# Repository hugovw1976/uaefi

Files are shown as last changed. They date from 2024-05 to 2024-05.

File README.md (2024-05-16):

# Ultra Affordable EFI

🟢[$100 base model rusEFI store](https://www.shop.rusefi.com/shop/p/uaefi-ultra-affordable-efi)🟢

## Community Support

🔴Community support ONLY 🔴 https://www.facebook.com/groups/rusEfi 🔴 [Discord](https://github.com/rusefi/rusefi/wiki/Discord)🔴

## Technical Details

Open Source KiCAD 7 hardware powered by [Hellen-One](https://github.com/andreika-git/hellen-one)

powerted by [rusEFI firmware](https://github.com/rusefi/rusefi)

[User Documentation](https://github.com/rusefi/rusefi/wiki/uaEFI)

x

x

## MCU options

1mg of flash is _required_.

One day we shall try https://jlcpcb.com/partdetail/Stmicroelectronics-STM32F427VIT6%2FC57097#EC or https://jlcpcb.com/partdetail/Stmicroelectronics-STM32F437VIT7%2FC1338578#EC

## rusEFI Store

https://www.shop.rusefi.com/shop/p/uaefi-ultra-affordable-efi

## HOWTO JLCPCB

You would need three files from ``boards/uaefi-a/board`` folder to place your JLCPB Assembly order: gerber.zip BOM-JLC.csv and CPL.csv

### Q: Something wrong with BOM?

A: Nope, that's normal nothing to worry about click 'Continue'.



### Q: how do I get more RAM for Lua?

A: fabricate with STM32F42xVI firmware would defect extra RAM and give you extra Lua. Once your script does not fit into STM32F42xVI it's F7 time or help us leverage F413.

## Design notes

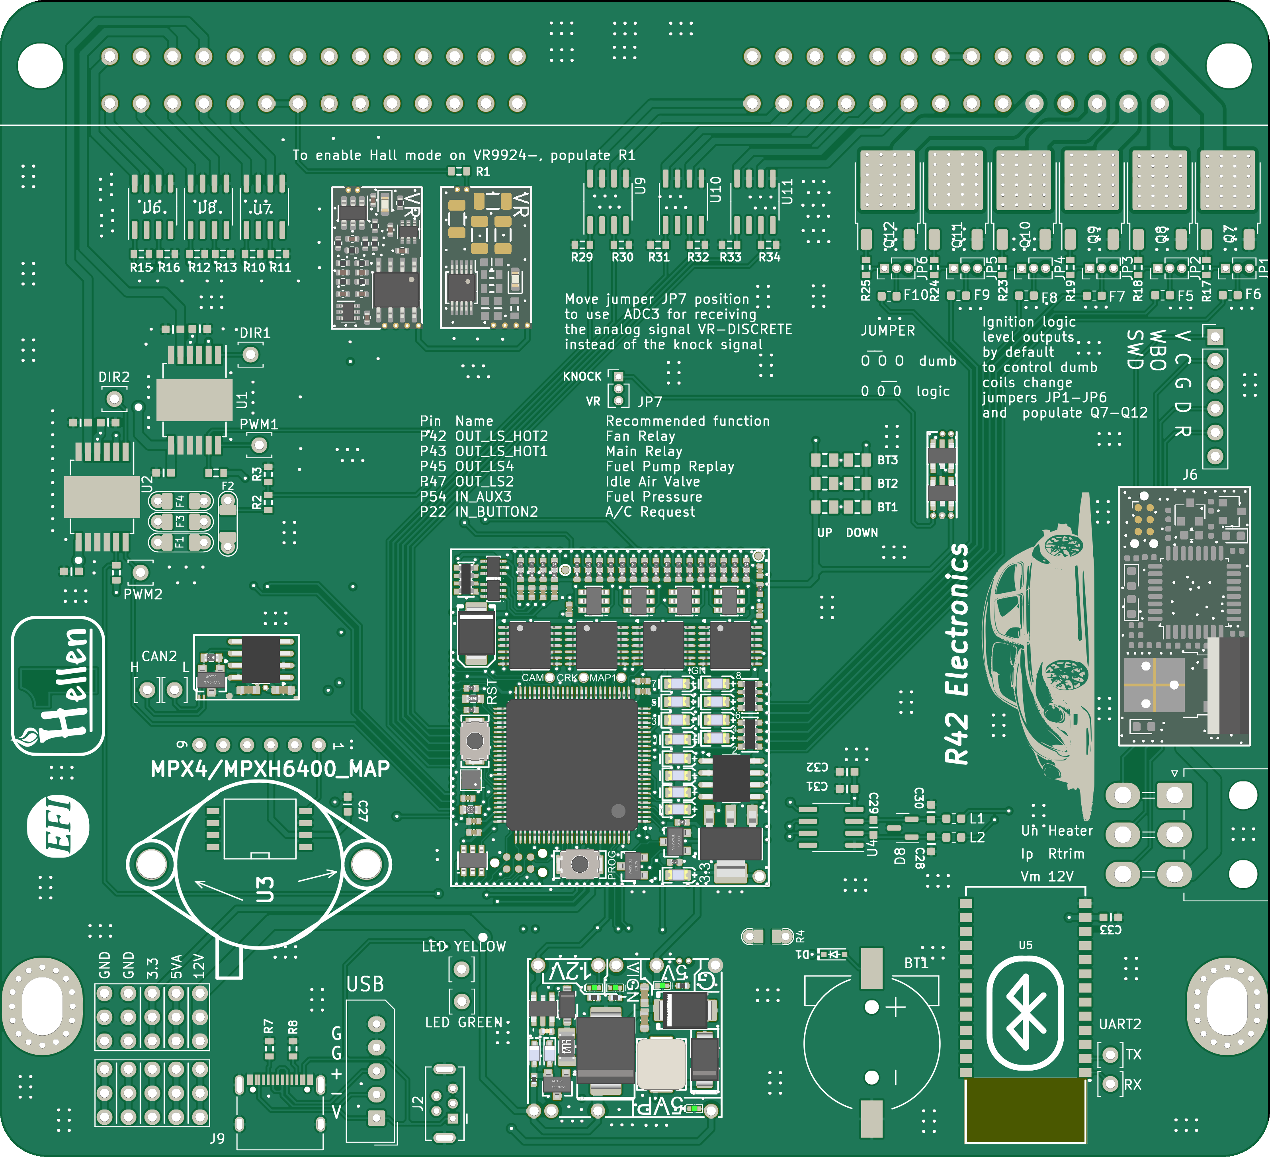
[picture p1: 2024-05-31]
boards/uaefi-d/board/uaefi-d.png

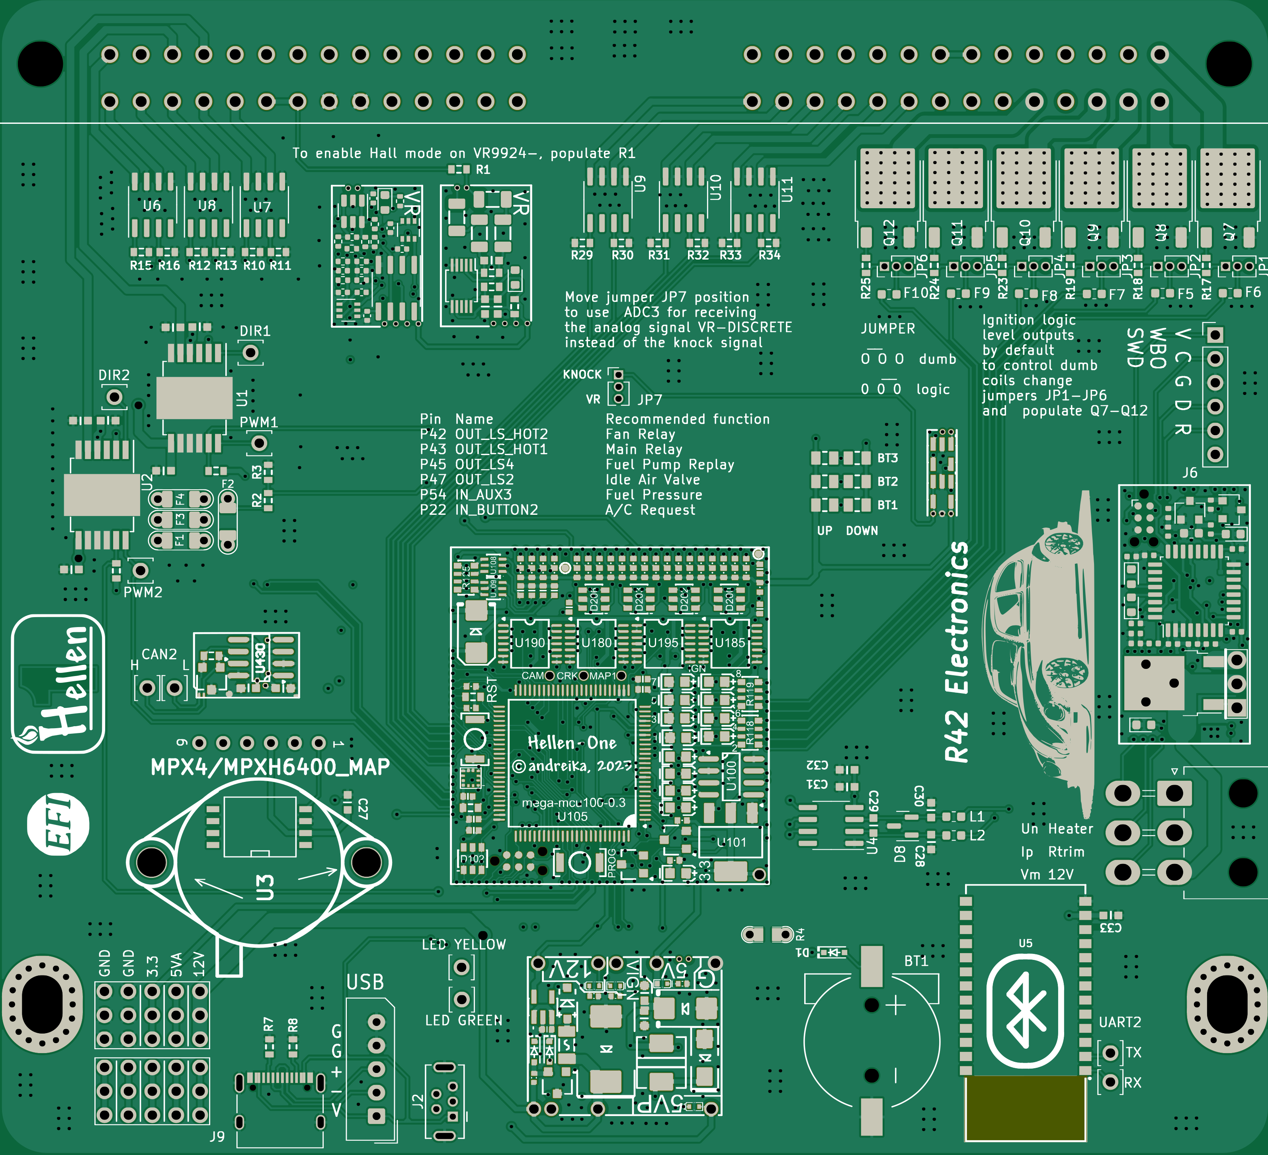
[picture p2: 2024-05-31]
boards/uaefi-d/board/misc/uaefi-d-top.png

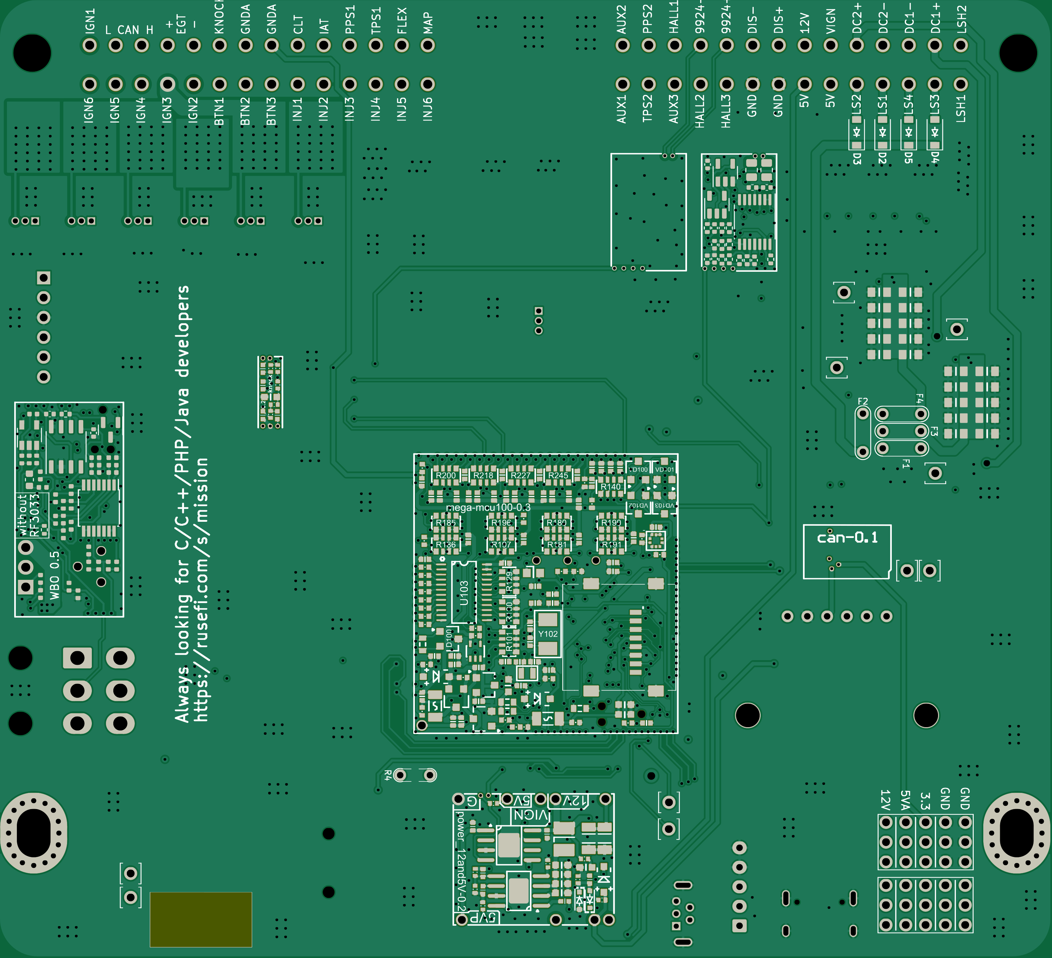
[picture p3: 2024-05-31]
boards/uaefi-d/board/misc/uaefi-d-bottom.png

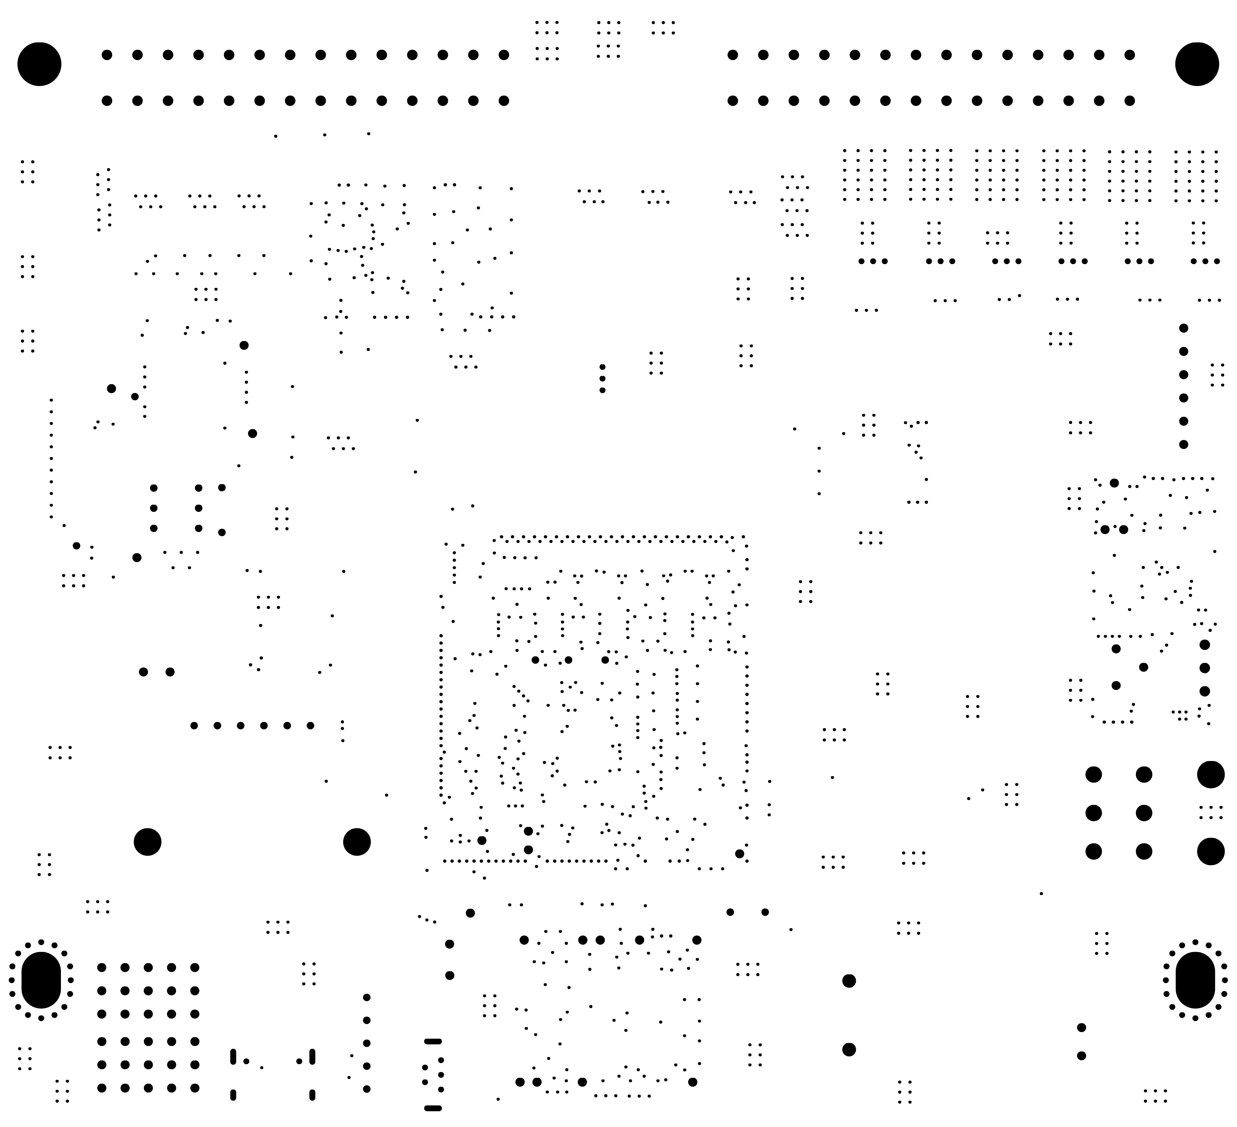
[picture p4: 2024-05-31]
boards/uaefi-d/board/misc/uaefi-d-outline.png

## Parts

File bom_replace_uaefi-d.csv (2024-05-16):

# remove +5V pull-ups from SPI1, because we use it with +3.3v accelerometer
R103,
R105,
# remove jumper resistor connecting BOOT1 with A22 input line, because we use STM32F4
R131,
#CAN wakeup disabled, O2S input enabled
R145,
#PWR_EN not used as GPIO
R142,
# DC-DC Inductor
L421,"MWSA0503S-100MT","MWSA0503","C408412"
L420,"NLCV32T-2R2M-EF","L1210","C295402"
# fuses
F410,"nSMD050-24V","SMD1206","C70076"
# TLS115
U411,"TLS115B0EJXUMA1","PG-DSO-8","C3747428"
#MAX9142
U754,"TLV3202AIDR","SO8","C129325"
# cost reduction
U106,
# DNP BLUETOOTH JDY
U5,
# STM32F407VGT6 is very cheap
U105,"STM32F407VGT6","LQFP100","C12345"
#20MHz crystal
Y102,"TXM20M0002503LFBEO00T","SMD5032-2P","C362485"
#SD Card
J100,"TF-014-H16","SMD","C125814"
#board ID capacitor shortage
C133,"1u","C0603","C113807"
#board ID fuse shortage
"F1, F2, F3, F4","12H1500D","PAD-1206-PAD","C140480"
#mux
"U755,U756","WAS3157B-6","SOT-363","C213161"
# DNP CONNECTOR
J3,
# Q1 options
# ZXMS6005SGTA C174042
# ZXMS6005DGTA C174045
# NCV8440ASTT3G C604063
# would VNL5160 work? would VNL5160 be the cheapest option?
# cost
"D6, D7, D411","PSM712-LF","SOT-23","C5180294"
#LEDs
"D751,D771,D601,D104,D108","GREEN_LED","LED0603","C965804"
"D602,D105,D109,D110,D111,D112,D113,D114,D115,D116","BLUE_LED","LED0603","C497940"
"LED1, LED2, LED3, LED4","BLUE_LED","LED0402","C2844007"
# same board ID as rev A for now!
#include hellen-one/board_id/generated/board_id_uaefi-a.csv
#include bom_pullups_uaefi-c.csv

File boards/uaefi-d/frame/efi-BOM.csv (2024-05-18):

Comment | Designator | Footprint | LCSC Part #
CR1220 | BT1 | CR1220-2 | C70381
10u | C1 | C0805 | C15850
10u | C2 | C0805 | C15850
10u | C3 | C0805 | C15850
10u | C4 | C0805 | C15850
10u | C5 | C0805 | C15850
10u | C6 | C0805 | C15850
10u | C7 | C0805 | C15850
10u | C8 | C0805 | C15850
10u | C9 | C0805 | C15850
10u | C10 | C0805 | C15850
100n | C11 | C0603 | C14663
10n | C12 | C0603 | C57112
10n | C13 | C0603 | C57112
10u | C14 | C0805 | C15850
10u | C15 | C0805 | C15850
10u | C16 | C0805 | C15850
10u | C17 | C0805 | C15850
10u | C18 | C0805 | C15850
10u | C19 | C0805 | C15850
10u | C20 | C0805 | C15850
10u | C21 | C0805 | C15850
10u | C22 | C0805 | C15850
10u | C23 | C0805 | C15850
100n | C24 | C0603 | C14663
10n | C25 | C0603 | C57112
10n | C26 | C0603 | C57112
100n | C27 | C0603 | C14663
10n | C28 | C0603 | C57112
100n | C29 | C0603 | C14663
10n | C30 | C0603 | C57112
100n | C31 | C0603 | C14663
1u | C32 | C0603 | C15849
100n | C33 | C0603 | C14663
1N4148WS | D1 | SOD-323 | C2128
B5819W | D2 | SOD-123 | C8598
B5819W | D3 | SOD-123 | C8598
B5819W | D4 | SOD-123 | C8598
B5819W | D5 | SOD-123 | C8598
NUP2105L | D8 | SOT-23 | C284104
12H1500D | F1 | PAD-1206-PAD | C182446
12H1500D | F2 | PAD-1206-PAD | C182446
12H1500D | F3 | PAD-1206-PAD | C182446
12H1500D | F4 | PAD-1206-PAD | C182446
50mA | F5 | Fuse_0603_1608Metric | C369141
50mA | F6 | Fuse_0603_1608Metric | C369141
50mA | F7 | Fuse_0603_1608Metric | C369141
50mA | F8 | Fuse_0603_1608Metric | C369141
50mA | F9 | Fuse_0603_1608Metric | C369141
50mA | F10 | Fuse_0603_1608Metric | C369141
RUSEFI_LOGO | G1 | rusefi_logo
LOGO | G2 | LOGO
PROTO_AREA | G3 | PROTO_AREA
PROTO_AREA | G4 | PROTO_AREA
M4 | H1 | MountingHole_4.3x6.2mm_M4_Pad_Via
M3 | H2 | MountingHole_4.3x6.2mm_M4_Pad_Via
211PL562L0011 | J1 | 211PL562L0011_2
USB_B_Mini | J2 | USB-MINI-B-VERTICAL
5569-06A2 | J3 | Molex_Mini-Fit_Jr_5569-06A2_2x03_P4.20mm_Horizontal | C293509
Conn_01x06 | J6 | PinHeader_1x06_P2.54mm_Vertical | C37208
Conn_01x05_Male | J7 | Molex_SPOX_5267-05A_1x05_P2.50mm_Vertical
USB_C | J9 | USB_C | C2927038
Jumper_3_Open | JP1 | PinHeader_1x03_P1.27mm_Vertical | C124354
Jumper_3_Open | JP2 | PinHeader_1x03_P1.27mm_Vertical | C124354
Jumper_3_Open | JP3 | PinHeader_1x03_P1.27mm_Vertical | C124354
Jumper_3_Open | JP4 | PinHeader_1x03_P1.27mm_Vertical | C124354
Jumper_3_Open | JP5 | PinHeader_1x03_P1.27mm_Vertical | C124354
Jumper_3_Open | JP6 | PinHeader_1x03_P1.27mm_Vertical | C124354
Jumper_3_Open | JP7 | PinHeader_1x03_P1.27mm_Vertical
470R@100MHz | L1 | L_0603_1608Metric | C97853
470R@100MHz | L2 | L_0603_1608Metric | C97853
Module:power_12and5V/0.2 | M1 | power_12and5V
Module:knock/0.2 | M2 | knock
Module:vr-discrete/0.5 | M3 | vr-discrete
Module:vr-max9924/0.1 | M4 | vr-max9924
Module:wbo/0.5 | M5 | wbo
Module:mega-mcu100/0.3 | M6 | mega-mcu100
Module:can/0.1 | M7 | can
Pad | P1 | PAD-TH
Pad | P2 | PAD-TH
Pad | P3 | PAD-TH
Pad | P4 | PAD-TH
Pad | P7 | PAD-TH
Pad | P8 | PAD-TH
Pad | P15 | PAD-TH
Pad | P16 | PAD-TH
Pad | P17 | PAD-TH
Pad | P18 | PAD-TH
ISL9V3040D3ST | Q7 | DPAK | C603080
ISL9V3040D3ST | Q8 | DPAK | C603080
ISL9V3040D3ST | Q9 | DPAK | C603080
ISL9V3040D3ST | Q10 | DPAK | C603080
ISL9V3040D3ST | Q11 | DPAK | C603080
ISL9V3040D3ST | Q12 | DPAK | C603080
4.7k | R1 | R0603
33k | R2 | R0603 | C4216
6.8k | R3 | R0603 | C23212
Jumper-Pad-Pad | R4 | PAD-0805-PAD | C17477
5.6k | R7 | R0603 | C23189
5.6k | R8 | R0603 | C23189
4.7k | R9 | R0603 | C23162
4.7k | R10 | R0603 | C23162
4.7k | R11 | R0603 | C23162
4.7k | R12 | R0603 | C23162
4.7k | R13 | R0603 | C23162
4.7k | R14 | R0603 | C23162
4.7k | R15 | R0603 | C23162
4.7k | R16 | R0603 | C23162
22 | R17 | R0603 | C23345
22 | R18 | R0603 | C23345
22 | R19 | R0603 | C23345
22 | R23 | R0603 | C23345
22 | R24 | R0603 | C23345
22 | R25 | R0603 | C23345
4.7k | R29 | R0603 | C23162
4.7k | R30 | R0603 | C23162
4.7k | R31 | R0603 | C23162
4.7k | R32 | R0603 | C23162
4.7k | R33 | R0603 | C23162
4.7k | R34 | R0603 | C23162
10k | R35 | R0805 | C17414
10k | R36 | R0805 | C17414
10k | R37 | R0805 | C17414
DNP | R38 | R0805
DNP | R39 | R0805
DNP | R40 | R0805
TLE9201SG | U1 | Infineon_PG-DSO-12-11 | C112633
TLE9201SG | U2 | Infineon_PG-DSO-12-11 | C112633
MPX4/MPXH6400_MAP | U3 | MPX-4_MAP
MAX31855KASA | U4 | SO8 | C52028
JDY-33 | U5 | JDY-33 | C9900001612
VNLD5160TR-E | U6 | SO8 | C377942
VNLD5160TR-E | U7 | SO8 | C377942
VNLD5160TR-E | U8 | SO8 | C377942
VNLD5160TR-E | U9 | SO8 | C377942
VNLD5160TR-E | U10 | SO8 | C377942
VNLD5160TR-E | U11 | SO8 | C377942

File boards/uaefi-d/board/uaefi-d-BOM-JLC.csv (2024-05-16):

Comment | Designator | Footprint | LCSC Part #
CR1220 | BT1 | CR1220-2 | C70381
10u | C1, C2, C3, C4, C5, C6, C7, C8, C9, C10, C14, C15, C16, C17, C18, C19, C20, C21, C22, C23 | C0805 | C15850
100n | C11, C24, C27, C29, C31, C33, C772, C430, C431 | C0603 | C14663
10n | C12, C13, C25, C26, C28, C30 | C0603 | C57112
1u | C32 | C0603 | C15849
1N4148WS | D1, D410, D412, D413, D414 | SOD-323 | C2128
B5819W | D2, D3, D4, D5, D416, D417, D101, D107 | SOD-123 | C8598
NUP2105L | D8 | SOT-23 | C284104
50mA | F5, F6, F7, F8, F9, F10 | Fuse_0603_1608Metric | C369141
Conn_01x06 | J6 | PinHeader_1x06_P2.54mm_Vertical | C37208
USB_C | J9 | USB_C | C2927038
Jumper_3_Open | JP1, JP2, JP3, JP4, JP5, JP6 | PinHeader_1x03_P1.27mm_Vertical | C124354
470R@100MHz | L1, L2 | L_0603_1608Metric | C97853
ISL9V3040D3ST | Q7, Q8, Q9, Q10, Q11, Q12 | DPAK | C603080
33k | R2, R120 | R0603 | C4216
6.8k | R3 | R0603 | C23212
Jumper-Pad-Pad | R4 | PAD-0805-PAD | C17477
5.6k | R7, R8 | R0603 | C23189
4.7k | R9, R10, R11, R12, R13, R14, R15, R16, R29, R30, R31, R32, R33, R34 | R0603 | C23162
22 | R17, R18, R19, R23, R24, R25 | R0603 | C23345
10k | R35, R36, R37, R752, R753 | R0805 | C17414
TLE9201SG | U1, U2 | Infineon_PG-DSO-12-11 | C112633
MAX31855KASA | U4 | SO8 | C52028
VNLD5160TR-E | U6, U7, U8, U9, U10, U11 | SO8 | C377942
47u | C410, C412 | C1206 | C96123
100n | C411, C413, C420, C470, C228 | C0402 | C307331
1u | C414, C415, C755, C758, C761, C762, C763, C765, C766, C767, C600, C607, C609, C610, C611 | C0402 | C52923
10u | C421, C422, C423, C424, C425, C426, C117 | C0603 | C96446
4.7u | C427, C616 | C0603 | C19666
10n | C428, C756, C757, C760, C764, C768, C769, C203, C202, C201, C200, C214, C215, C225, C226, C227 | C0402 | C15195
220p | C429 | C0402 | C1530
SMCJ30A | D418 | SMC | C310046
SS34 | D420 | SMA | C8678
P6SMB6.8CA | D421, D205 | SMB | C78395
6.8k | R410, R413 | R0402 | C25917
33k | R411, R424, R425, R474 | R0402 | C25779
1 | R420 | R0402 | C25086
10k | R421, R426, R427, R757, R762, R763, R767, R768, R604, R605, R613, R614, R618, R619, R625, R102, R107, R108, R109, R121, R127, R128, R141, R219 | R0402 | C25744
68k | R422, R760, R602, R603 | R0402 | C36871
12k | R423, R472, R754 | R0402 | C25752
4.7k | R428, R144, R202, R201, R124, R126, R132 | R0402 | C25900
MIC5205-3.3YM5 | U410 | SOT23-5 | C37970
LMR14020 | U420 | SOP8 | C187824
3.3n | C471 | C0402 | C26404
330p | C472 | C0402 | C13533
47p | C473 | C0402 | C1567
680p | C474 | C0603 | C1630
470k | R470 | R0402 | C25790
100k | R471, R473, R755, R756, R758, R759, R615, R621 | R0402 | C25741
LMV321IDBVR | U470, U471 | SOT23-5 | C7972
1n | C751, C135, C139, C141, C142, C211, C209, C208, C212, C213, C210, C143, C144, C145, C146 | C0402 | C1523
470n | C752 | C0402 | C47339
100n | C753, C754, C759, C601, C602, C605, C608, C612, C613, C614, C615, C617, C618, C100, C101, C105, C108, C111, C112, C113, C119, C120, C122, C124, C126, C127, C130, C134, C147, C180, C185, C190, C195, C220, C221, C222 | C0402 | C1525
2.2k | R751, R122, R123, R146, R147 | R0402 | C25879
10 | R761, R764, R769, R606, R110, R111, R112, R113, R114, R115, R116, R117 | R0402 | C25077
1k | R765, R766, R600, R601, R616, R617, R622, R626, R627, R628 | R0402 | C11702
SRV05-4-P-T7 | U751, D102, D200, D202, D203, D206 | SOT23-6 | C85364
74AHC1G02 | U752, U757 | SOT23-5 | C7463
MCP6004 | U753, U600, U180, U185, U190, U195 | TSSOP14 | C50282
1n | C771 | C0603 | C1588
22u | C773 | C0603 | C59461
4.7k | R771, R772, R773, R774 | R1206 | C17936
10k | R776, R777, R134 | R0603 | C25804
MAX9924UAUB+ | U771 | MSOP-10_3x3mm_P0.5mm | C143633
33n | C603 | C0402 | C1585
LED-RED-0603 | D600, D603, D103 | LED-0603 | C2286
PESD1CAN | D604, D100, D430 | SOT-23 | C343993
VND7NV04TR-E | Q600 | DPAK | C155605
22k | R607 | R0402 | C25768
47 | R608 | R0402 | C25118
61.9 | R609 | R0603 | C23092
20k | R610, R611, R612 | R0402 | C25765
27k | R620, R623 | R0402 | C25771
3.3k | R624 | R0402 | C25890
AD8628 | U601 | TSOT23-5 | C29309
STM32F042K6Tx | U602 | LQFP32 | C69216
REF3033 | U603, U102 | SOT-23 | C36658
XC6206P332MR | U604 | SOT-23 | C5446
TJA1051T/3/1J | U605, U100, U430 | SO8 | C38695
SN74LVC4245APWR | U103 | TSSOP24 | C7859
SN74LVC1G06DCKR | U110 | SOT-353 | C7828
SMD1206B035TF/16 | F100, F101 | R1206 | C269114
LPS22HBTR | U107 | HLGA-10L | C94049
LED-YELLOW-0603 | D106 | LED-0603 | C72038
LDL1117S33R | U101 | SOT-223 | C435835
BTN | S100, S101 | SMD-2_2.9x3.9x1.7 | C115357
BLM18AG601SN1D | L100 | L0603 | C19330
BAT54S | VD100, VD101, VD102, VD103 | SOT-23 | C47546
AO3401A | Q100, Q102 | SOT-23 | C15127
AO3400A | Q101, Q103 | SOT-23 | C20917
680k | R222, R220, R208, R207, R234, R235, R232, R233, R250, R251, R252, R225, R135 | R0402 | C163456
510 | R254, R255, R256, R258 | R0402 | C25123
470 | R101, R118, R119 | R0603-4 | C25510
120 | R100, R430 | R0603 | C22787
100 | R104, R106 | R0603 | C22775
74LVC2G17GW,125 | U108, U109 | SOT-363 | C80500
32.768 kHz | Y101 | SMD2012 | C99009
18p | C132, C136 | C0402 | C1549
12p | C115, C116 | C0402 | C1547
10k | R129, R130, R140 | R0603-4 | C29718
5.1k | R195 | R0402 | C25905
4.7u | C102, C103, C104, C106, C107, C137, C138, C140 | C0402 | C23733
4.7k | R125, R180, R181, R185, R186, R190, R191, R196, R197, R200, R218, R227, R245 | R0603-4 | C66697
2.2u | C114, C131, C223, C224, C229 | C0402 | C12530
0 | R143, R148 | R0402 | C17168
MWSA0503S-100MT | L421 | MWSA0503 | C408412
NLCV32T-2R2M-EF | L420 | L1210 | C295402
nSMD050-24V | F410 | SMD1206 | C70076
TLS115B0EJXUMA1 | U411 | PG-DSO-8 | C3747428
TLV3202AIDR | U754 | SO8 | C129325
STM32F407VGT6 | U105 | LQFP100 | C12345
TXM20M0002503LFBEO00T | Y102 | SMD5032-2P | C362485
TF-014-H16 | J100 | SMD | C125814
1u | C133 | C0603 | C113807
12H1500D | F1, F2, F3, F4 | PAD-1206-PAD | C140480
WAS3157B-6 | U755, U756 | SOT-363 | C213161
PSM712-LF | D6, D7, D411 | SOT-23 | C5180294
GREEN_LED | D751, D771, D601, D104, D108 | LED0603 | C965804
BLUE_LED | D602, D105, D109, D110, D111, D112, D113, D114, D115, D116 | LED0603 | C497940
BLUE_LED | LED1, LED2, LED3, LED4 | LED0402 | C2844007
750 | R133 | R0603 | C23241

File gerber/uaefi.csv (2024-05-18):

Comment | Designator | Footprint | LCSC Part #
CR1220 | BT1 | kicad6-libraries:CR1220-2 | C70381
10u | C1 | hellen-one-common:C0805 | C15850
10u | C2 | hellen-one-common:C0805 | C15850
10u | C3 | hellen-one-common:C0805 | C15850
10u | C4 | hellen-one-common:C0805 | C15850
10u | C5 | hellen-one-common:C0805 | C15850
10u | C6 | hellen-one-common:C0805 | C15850
10u | C7 | hellen-one-common:C0805 | C15850
10u | C8 | hellen-one-common:C0805 | C15850
10u | C9 | hellen-one-common:C0805 | C15850
10u | C10 | hellen-one-common:C0805 | C15850
100n | C11 | hellen-one-common:C0603 | C14663
10n | C12 | hellen-one-common:C0603 | C57112
10n | C13 | hellen-one-common:C0603 | C57112
10u | C14 | hellen-one-common:C0805 | C15850
10u | C15 | hellen-one-common:C0805 | C15850
10u | C16 | hellen-one-common:C0805 | C15850
10u | C17 | hellen-one-common:C0805 | C15850
10u | C18 | hellen-one-common:C0805 | C15850
10u | C19 | hellen-one-common:C0805 | C15850
10u | C20 | hellen-one-common:C0805 | C15850
10u | C21 | hellen-one-common:C0805 | C15850
10u | C22 | hellen-one-common:C0805 | C15850
10u | C23 | hellen-one-common:C0805 | C15850
100n | C24 | hellen-one-common:C0603 | C14663
10n | C25 | hellen-one-common:C0603 | C57112
10n | C26 | hellen-one-common:C0603 | C57112
100n | C27 | hellen-one-common:C0603 | C14663
10n | C28 | hellen-one-common:C0603 | C57112
100n | C29 | hellen-one-common:C0603 | C14663
10n | C30 | hellen-one-common:C0603 | C57112
100n | C31 | hellen-one-common:C0603 | C14663
1u | C32 | hellen-one-common:C0603 | C15849
100n | C33 | hellen-one-common:C0603 | C14663
1N4148WS | D1 | hellen-one-common:SOD-323 | C2128
B5819W | D2 | hellen-one-common:SOD-123 | C8598
B5819W | D3 | hellen-one-common:SOD-123 | C8598
B5819W | D4 | hellen-one-common:SOD-123 | C8598
B5819W | D5 | hellen-one-common:SOD-123 | C8598
NUP2105L | D8 | Package_TO_SOT_SMD:SOT-23 | C284104
12H1500D | F1 | hellen-one-common:PAD-1206-PAD | C182446
12H1500D | F2 | hellen-one-common:PAD-1206-PAD | C182446
12H1500D | F3 | hellen-one-common:PAD-1206-PAD | C182446
12H1500D | F4 | hellen-one-common:PAD-1206-PAD | C182446
50mA | F5 | Fuse:Fuse_0603_1608Metric | C369141
50mA | F6 | Fuse:Fuse_0603_1608Metric | C369141
50mA | F7 | Fuse:Fuse_0603_1608Metric | C369141
50mA | F8 | Fuse:Fuse_0603_1608Metric | C369141
50mA | F9 | Fuse:Fuse_0603_1608Metric | C369141
50mA | F10 | Fuse:Fuse_0603_1608Metric | C369141
RUSEFI_LOGO | G1 | kicad6-libraries:rusefi_logo
LOGO | G2 | hellen-one-common:LOGO
PROTO_AREA | G3 | hellen-one-common:PROTO_AREA
PROTO_AREA | G4 | hellen-one-common:PROTO_AREA
M4 | H1 | MountingHole:MountingHole_4.3x6.2mm_M4_Pad_Via
M3 | H2 | MountingHole:MountingHole_4.3x6.2mm_M4_Pad_Via
211PL562L0011 | J1 | uaefi-main:211PL562L0011_2
USB_B_Mini | J2 | hellen-one-common:USB-MINI-B-VERTICAL
5569-06A2 | J3 | Connector_Molex:Molex_Mini-Fit_Jr_5569-06A2_2x03_P4.20mm_Horizontal | C293509
Conn_01x06 | J6 | Connector_PinHeader_2.54mm:PinHeader_1x06_P2.54mm_Vertical | C37208
Conn_01x05_Male | J7 | Connector_Molex:Molex_SPOX_5267-05A_1x05_P2.50mm_Vertical
USB_C | J9 | kicad6-libraries:USB_C | C2927038
Jumper_3_Open | JP1 | Connector_PinHeader_1.27mm:PinHeader_1x03_P1.27mm_Vertical | C124354
Jumper_3_Open | JP2 | Connector_PinHeader_1.27mm:PinHeader_1x03_P1.27mm_Vertical | C124354
Jumper_3_Open | JP3 | Connector_PinHeader_1.27mm:PinHeader_1x03_P1.27mm_Vertical | C124354
Jumper_3_Open | JP4 | Connector_PinHeader_1.27mm:PinHeader_1x03_P1.27mm_Vertical | C124354
Jumper_3_Open | JP5 | Connector_PinHeader_1.27mm:PinHeader_1x03_P1.27mm_Vertical | C124354
Jumper_3_Open | JP6 | Connector_PinHeader_1.27mm:PinHeader_1x03_P1.27mm_Vertical | C124354
Jumper_3_Open | JP7 | Connector_PinHeader_1.27mm:PinHeader_1x03_P1.27mm_Vertical
470R@100MHz | L1 | Inductor_SMD:L_0603_1608Metric | C97853
470R@100MHz | L2 | Inductor_SMD:L_0603_1608Metric | C97853
Module-power_12and5V-0.2 | M1 | hellen-one-power_12and5V-0.2:power_12and5V
Module-knock-0.2 | M2 | hellen-one-knock-0.2:knock
Module-vr-discrete-0.5 | M3 | hellen-one-vr-discrete-0.5:vr-discrete
Module-vr-max9924-0.1 | M4 | hellen-one-vr-max9924-0.1:vr-max9924
Module-wbo-0.5 | M5 | hellen-one-wbo-0.5:wbo
Module:mega-mcu100/0.3 | M6 | hellen-one-mega-mcu100-0.3:mega-mcu100
Module-can-0.1 | M7 | hellen-one-can-0.1:can
Pad | P1 | hellen-one-common:PAD-TH
Pad | P2 | hellen-one-common:PAD-TH
Pad | P3 | hellen-one-common:PAD-TH
Pad | P4 | hellen-one-common:PAD-TH
Pad | P7 | hellen-one-common:PAD-TH
Pad | P8 | hellen-one-common:PAD-TH
Pad | P15 | hellen-one-common:PAD-TH
Pad | P16 | hellen-one-common:PAD-TH
Pad | P17 | hellen-one-common:PAD-TH
Pad | P18 | hellen-one-common:PAD-TH
ISL9V3040D3ST | Q7 | Package_TO_SOT_SMD:TO-252-2 | C603080
ISL9V3040D3ST | Q8 | Package_TO_SOT_SMD:TO-252-2 | C603080
ISL9V3040D3ST | Q9 | Package_TO_SOT_SMD:TO-252-2 | C603080
ISL9V3040D3ST | Q10 | Package_TO_SOT_SMD:TO-252-2 | C603080
ISL9V3040D3ST | Q11 | Package_TO_SOT_SMD:TO-252-2 | C603080
ISL9V3040D3ST | Q12 | Package_TO_SOT_SMD:TO-252-2 | C603080
4.7k | R1 | hellen-one-common:R0603
33k | R2 | hellen-one-common:R0603 | C4216
6.8k | R3 | hellen-one-common:R0603 | C23212
Jumper-Pad-Pad | R4 | hellen-one-common:PAD-0805-PAD | C17477
5.6k | R7 | hellen-one-common:R0603 | C23189
5.6k | R8 | hellen-one-common:R0603 | C23189
4.7k | R9 | hellen-one-common:R0603 | C23162
4.7k | R10 | hellen-one-common:R0603 | C23162
4.7k | R11 | hellen-one-common:R0603 | C23162
4.7k | R12 | hellen-one-common:R0603 | C23162
4.7k | R13 | hellen-one-common:R0603 | C23162
4.7k | R14 | hellen-one-common:R0603 | C23162
4.7k | R15 | hellen-one-common:R0603 | C23162
4.7k | R16 | hellen-one-common:R0603 | C23162
22 | R17 | hellen-one-common:R0603 | C23345
22 | R18 | hellen-one-common:R0603 | C23345
22 | R19 | hellen-one-common:R0603 | C23345
22 | R23 | hellen-one-common:R0603 | C23345
22 | R24 | hellen-one-common:R0603 | C23345
22 | R25 | hellen-one-common:R0603 | C23345
4.7k | R29 | hellen-one-common:R0603 | C23162
4.7k | R30 | hellen-one-common:R0603 | C23162
4.7k | R31 | hellen-one-common:R0603 | C23162
4.7k | R32 | hellen-one-common:R0603 | C23162
4.7k | R33 | hellen-one-common:R0603 | C23162
4.7k | R34 | hellen-one-common:R0603 | C23162
10k | R35 | hellen-one-common:R0805 | C17414
10k | R36 | hellen-one-common:R0805 | C17414
10k | R37 | hellen-one-common:R0805 | C17414
DNP | R38 | hellen-one-common:R0805
DNP | R39 | hellen-one-common:R0805
DNP | R40 | hellen-one-common:R0805
TLE9201SG | U1 | Package_SO:Infineon_PG-DSO-12-11 | C112633
TLE9201SG | U2 | Package_SO:Infineon_PG-DSO-12-11 | C112633
MPX4/MPXH6400_MAP | U3 | kicad6-libraries:MPX-4_MAP
MAX31855KASA | U4 | Package_SO:SOIC-8_3.9x4.9mm_P1.27mm | C52028
JDY-33 | U5 | kicad6-libraries:JDY-33 | C9900001612
VNLD5160TR-E | U6 | Package_SO:SOIC-8_3.9x4.9mm_P1.27mm | C377942
VNLD5160TR-E | U7 | Package_SO:SOIC-8_3.9x4.9mm_P1.27mm | C377942
VNLD5160TR-E | U8 | Package_SO:SOIC-8_3.9x4.9mm_P1.27mm | C377942
VNLD5160TR-E | U9 | Package_SO:SOIC-8_3.9x4.9mm_P1.27mm | C377942
VNLD5160TR-E | U10 | Package_SO:SOIC-8_3.9x4.9mm_P1.27mm | C377942
VNLD5160TR-E | U11 | Package_SO:SOIC-8_3.9x4.9mm_P1.27mm | C377942

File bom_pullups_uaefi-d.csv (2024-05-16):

#CRANK BUTTON1: UP 680k 1n
R222 | 680k | R0402 | C163456
R226
C211 | 1n | C0402 | C1523
#CAM BUTTON2: UP 680k 1n
R220 | 680k | R0402 | C163456
R224
C209 | 1n | C0402 | C1523
#VSS FLEX: UP 10k 1n
R219 | 10k | R0402 | C25744
R223
C208 | 1n | C0402 | C1523
#TPS TPS1: DOWN 680k 10n
R204
R208 | 680k | R0402 | C163456
C203 | 10n | C0402 | C15195
#PPS PPS1: DOWN 680k 10n
R203
R207 | 680k | R0402 | C163456
C202 | 10n | C0402 | C15195
#IAT IAT: UP 4.7k 10n
R202 | 4.7k | R0402 | C25900
R206
C201 | 10n | C0402 | C15195
#CLT CLT: UP 4.7k 10n
R201 | 4.7k | R0402 | C25900
R205
C200 | 10n | C0402 | C15195
#O2S AUX1: DOWN 680k 10n
R230
R234 | 680k | R0402 | C163456
C214 | 10n | C0402 | C15195
#O2S2 AUX2: DOWN 680k 10n
R231
R235 | 680k | R0402 | C163456
C215 | 10n | C0402 | C15195
#MAP1 MAP: DOWN 680k 1n
R228
R232 | 680k | R0402 | C163456
C212 | 1n | C0402 | C1523
#MAP2 INTERNAL_MAP: DOWN 680k 1n
R229
R233 | 680k | R0402 | C163456
C213 | 1n | C0402 | C1523
#AUX1 TPS2: DOWN 680k 10n
R246
R250 | 680k | R0402 | C163456
C225 | 10n | C0402 | C15195
#AUX2 PPS2: DOWN 680k 10n
R247
R251 | 680k | R0402 | C163456
C226 | 10n | C0402 | C15195
#AUX3 AUX3: DOWN 680k 10n
R248
R252 | 680k | R0402 | C163456
C227 | 10n | C0402 | C15195
#AUX4 VMAIN: DOWN DNP 100n
R249
R253
C228 | 100n | C0402 | C307331
#KNOCK KNOCK: DOWN 680k 1n
R221
R225 | 680k | R0402 | C163456
C210 | 1n | C0402 | C1523
#D1 HALL1: UP 4.7k 1n
R124 | 4.7k | R0402 | C25900
R136
C143 | 1n | C0402 | C1523
#D2 HALL2: UP 4.7k 1n
R126 | 4.7k | R0402 | C25900
R137
C144 | 1n | C0402 | C1523
#D3 HALL3: UP 4.7k 1n
R132 | 4.7k | R0402 | C25900
R138
C145 | 1n | C0402 | C1523
#D4 BUTTON3: UP 680k 1n
R135 | 680k | R0402 | C163456
R139
C146 | 1n | C0402 | C1523

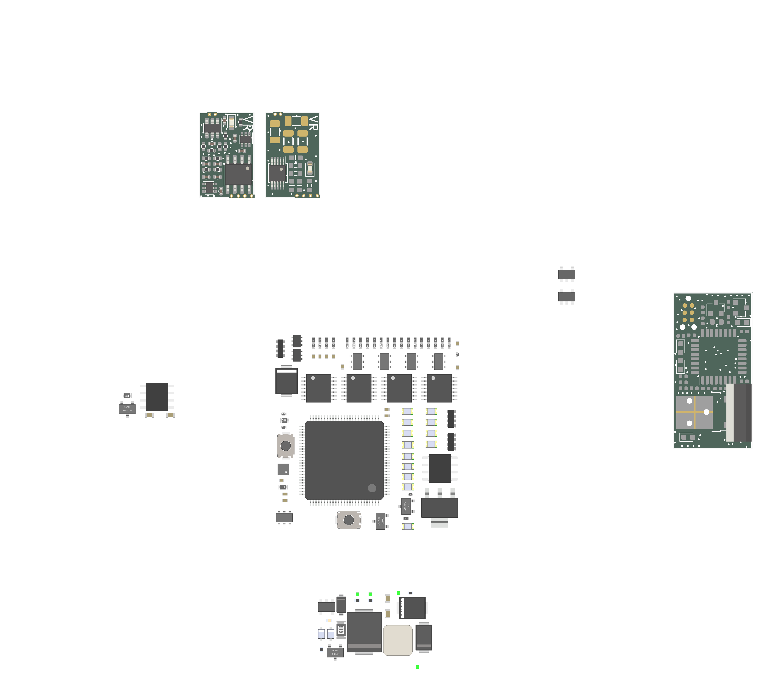
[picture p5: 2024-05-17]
boards/uaefi-d/board/misc/uaefi-d-components.png

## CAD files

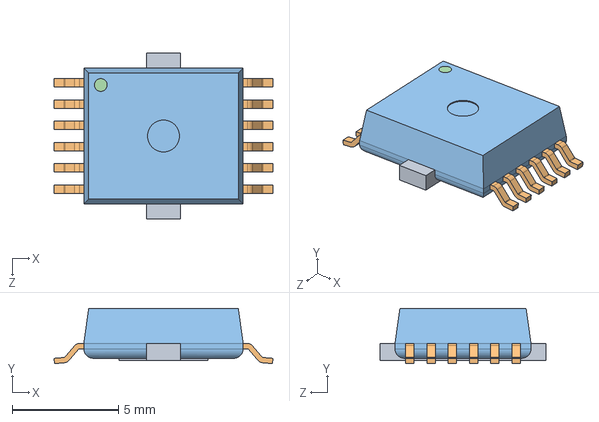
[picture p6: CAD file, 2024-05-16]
3D models/TLE9201SG.STEP
10.3 x 2.60 x 7.80 mm

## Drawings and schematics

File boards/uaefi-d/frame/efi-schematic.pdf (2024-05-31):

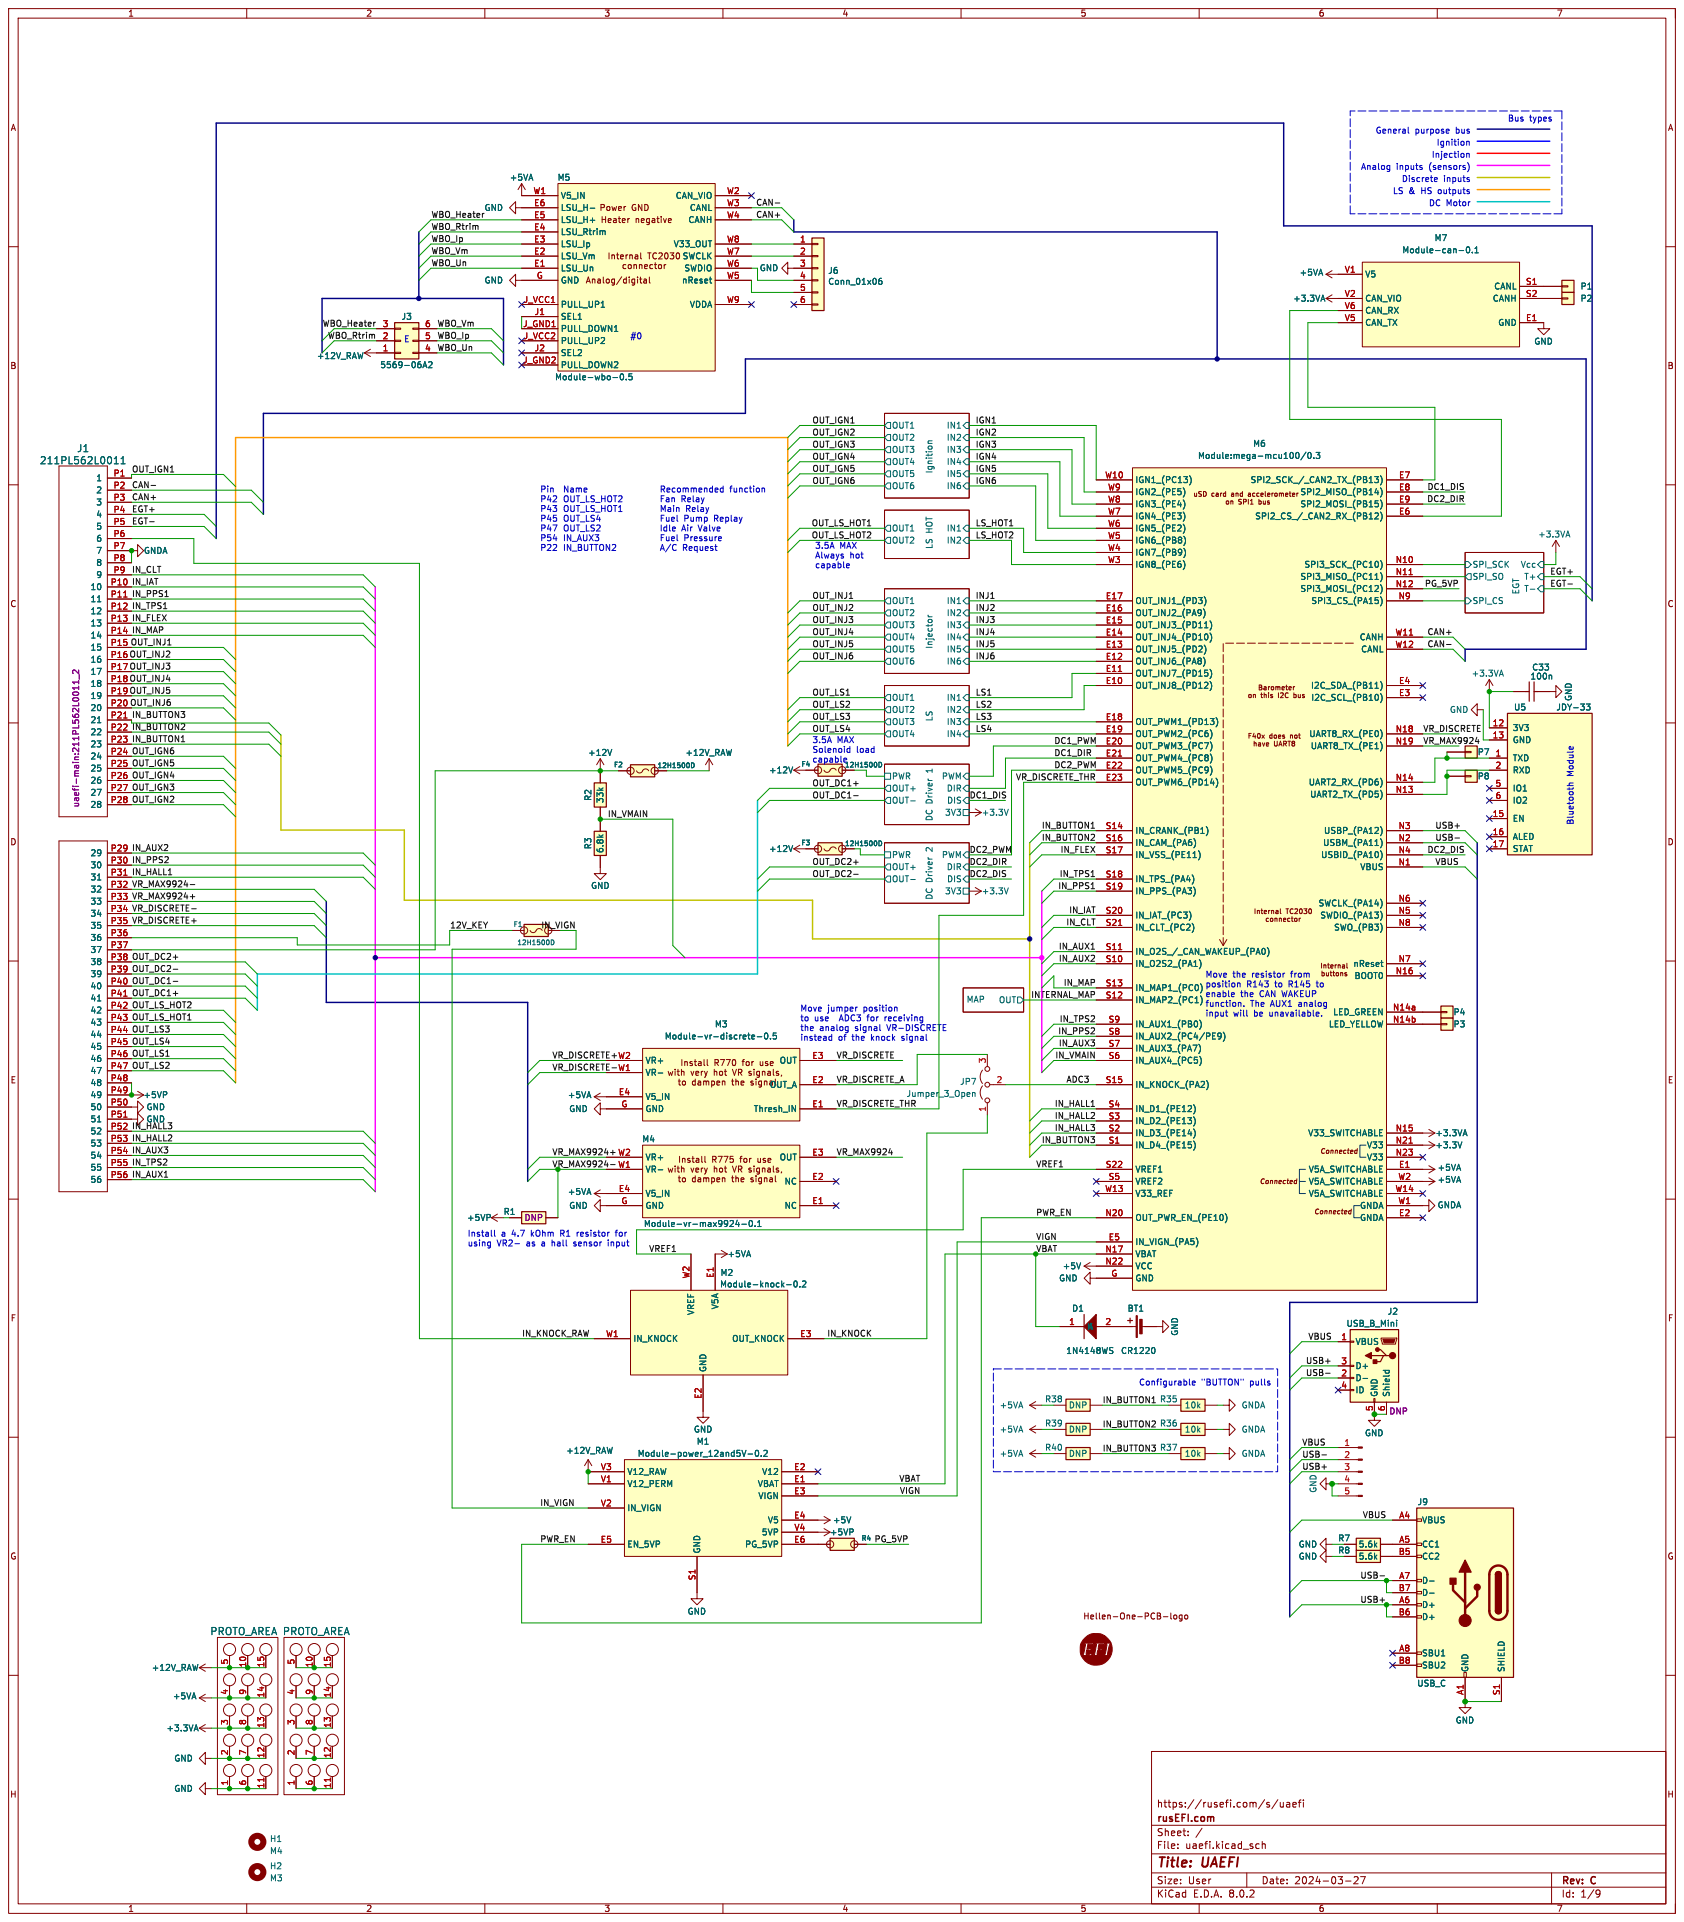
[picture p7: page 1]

Analog/digital Heater negative Power GND

3V3 12 GND 13 EN 15 ALED 16 STAT 17 RXD 2

P7P8 GND

enable the CAN WAKEUP

the analog signal VR-DISCRETE
instead of the knock signal

VREF1 VR_DISCRETE_THR
BT1 CR1220 R38 DNPHellen-One-PCB-logo R39 DNP R40 DNP

https://rusefi.com/s/uaefi
Id: 1/9 Title: UAEFI File: uaefi.kicad_sch Sheet: / rusEFI.com

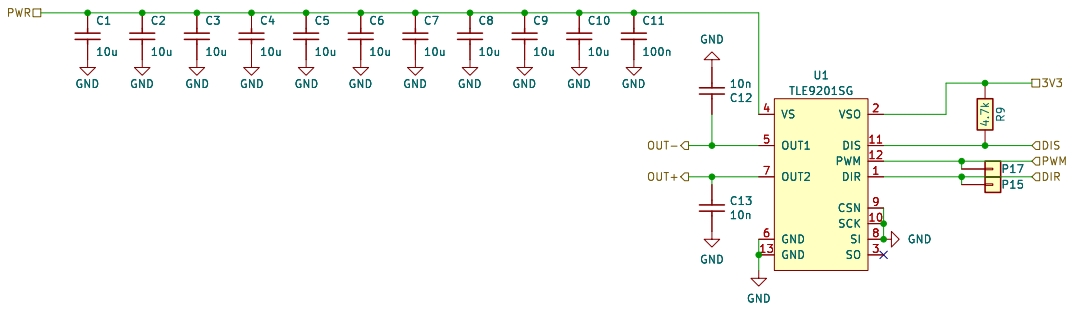
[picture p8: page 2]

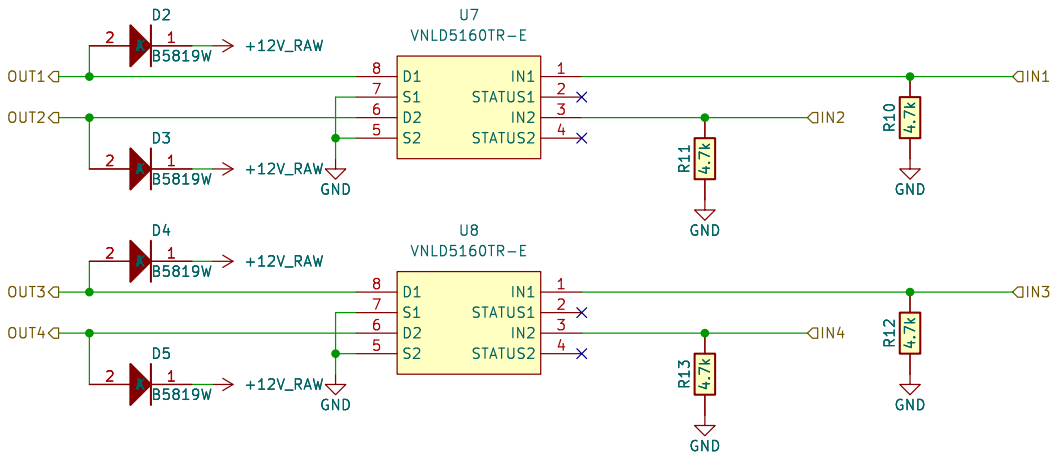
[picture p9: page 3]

File: LS4.kicad_sch Sheet: /LS/ rusefi.com

Id: 3/9 Title: UAEFI Low Side

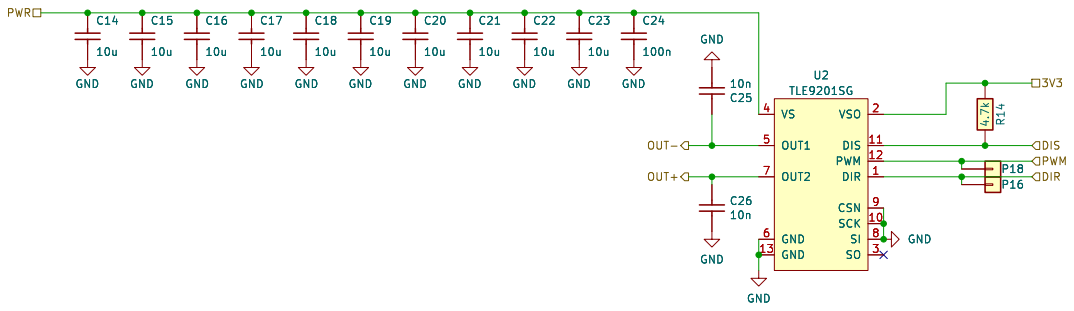
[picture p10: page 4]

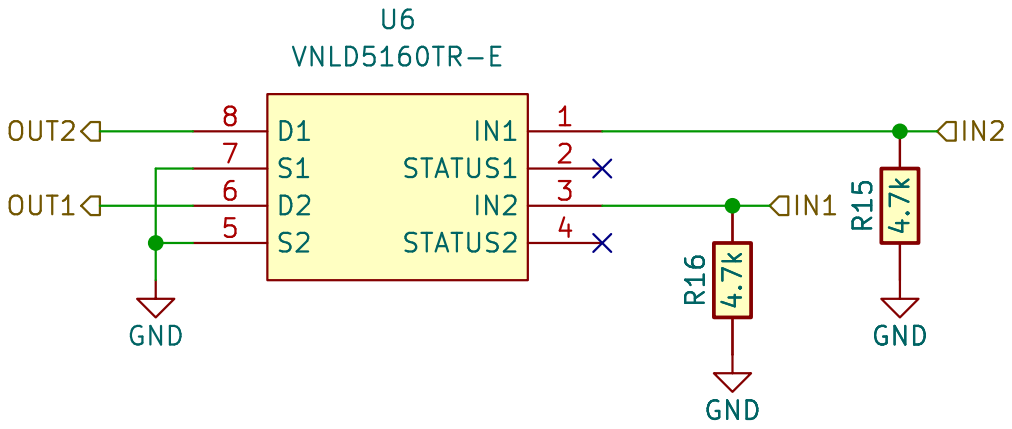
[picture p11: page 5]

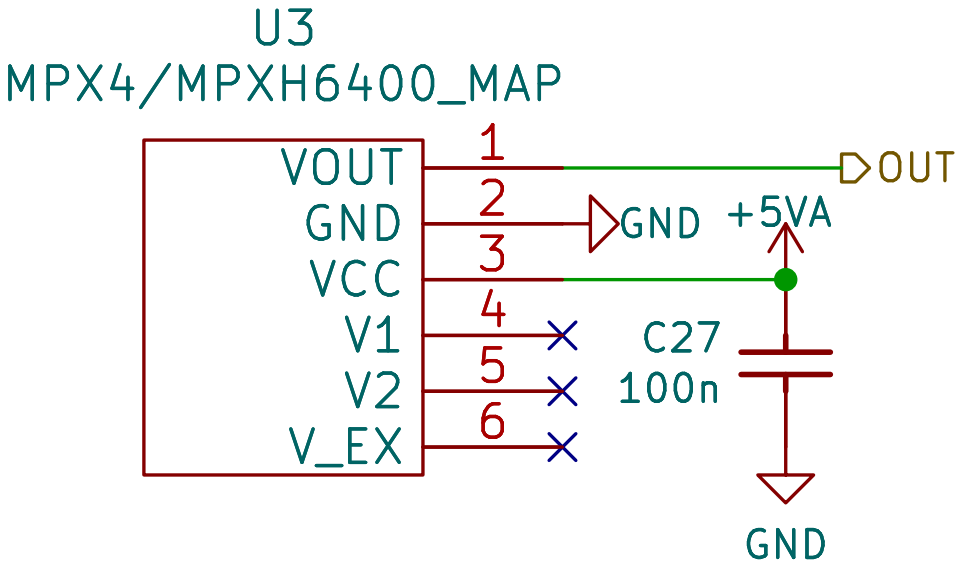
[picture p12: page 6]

Id: 8/9 Title: File: MAP.kicad_sch Sheet: /MAP/

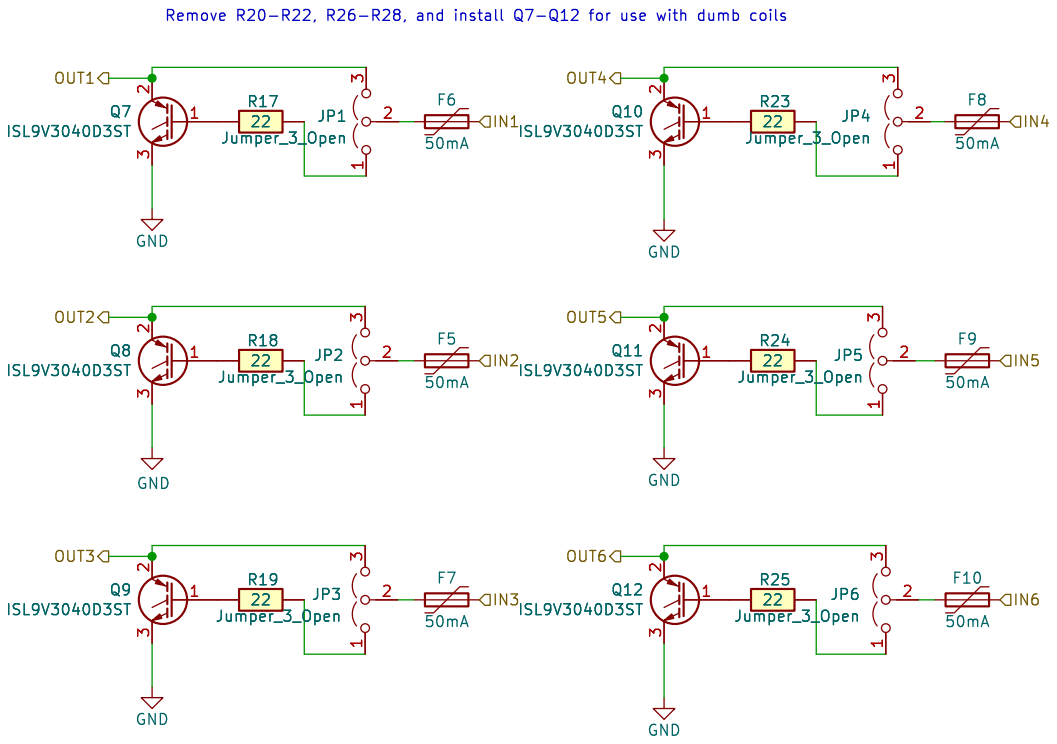
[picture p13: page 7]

File: IGN6.kicad_sch Sheet: /Ignition/ rusefi.com

Id: 9/9 Title: UAEFI Ignition

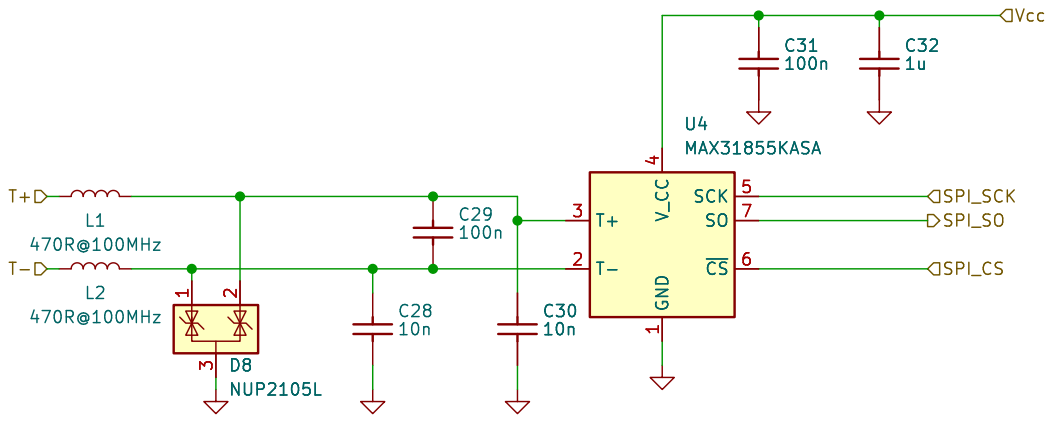
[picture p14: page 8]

Id: 9/9 Title: File: egt.kicad_sch Sheet: /EGT/

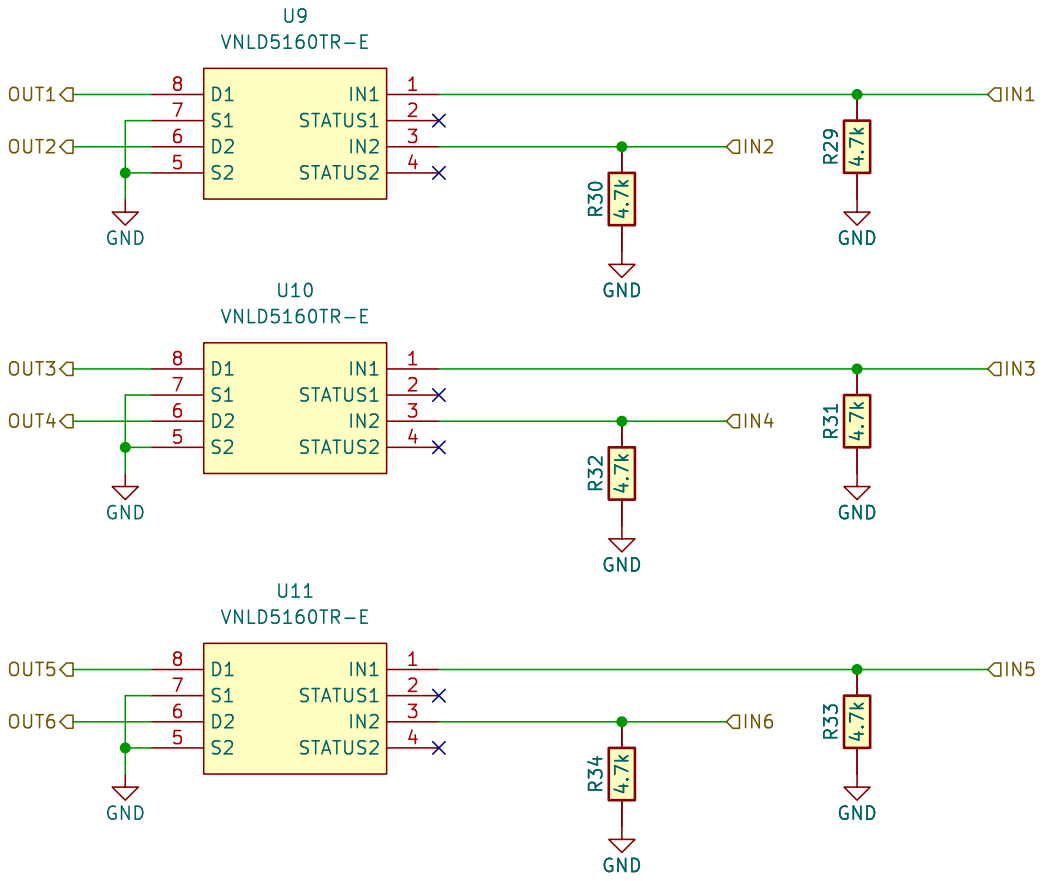
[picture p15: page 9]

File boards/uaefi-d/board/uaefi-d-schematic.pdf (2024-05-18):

100n GND E1 CANL S1 CANH S2 V5 V1 CAN_VIO V2 CAN_TX V5 CAN_RX V6 | M7 Module-can-0.1 | GND
9 | P9 J1


Analog/digital Heater negative Power GND

3V3 12 GND 13 EN 15 ALED 16 STAT 17 RXD 2

P7P8 GND

enable the CAN WAKEUP

the analog signal VR-DISCRETE
instead of the knock signal

VREF1 VR_DISCRETE_THR
BT1 CR1220 R38 DNPHellen-One-PCB-logo R39 DNP R40 DNP

https://rusefi.com/s/uaefi
Id: 1/9 Title: UAEFI File: uaefi.kicad_sch Sheet: / rusEFI.com


D Date: 2023-11-01 KiCad; E.D.A. 8.0.2 Size: A4; Rev:; GND; +12V_RAW; GND GND; GND R¹² 4.7k; R¹¹ 4.7k +12V_RAW; R¹³ 4.7k GND; 1 STATUS1; 3 STATUS2; U8 VNLD5160TR-E; U7 VNLD5160TR-E; R¹⁰ 4.7k; OUT1 OUT4 OUT3; IN1 OUT2; R¹⁰ 4.7k GND GND R¹³ 4.7k GND R¹¹ 4.7k; R¹² 4.7k GND

File: LS4.kicad_sch Sheet: /LS/ rusefi.com

Id: 3/9 Title: UAEFI Low Side

D Date: 2023-11-01 KiCad; E.D.A. 8.0.2 Size: A4; Rev:; Id: 6/9 Title: UAEF Low Side always hot File: LS_HOT.kicad_sch Sheet: /LS; HOT/ rusefi.com; GND R¹⁶ 4.7k GND; R¹⁵ 4.7k; 1 STATUS1; 3 STATUS2; U6 VNLD5160TR-E GND; IN2 OUT1 OUT2; R¹⁵ 4.7k GND R¹⁶ 4.7k; GND

D Date: KiCad; E.D.A. 8.0.2 Size: A4; Rev:; VOUT; 1 GND; 2 VCC; 6 U3 MPX4/MPXH6400_MAP; GND GND; OUT U3 MPX4/MPXH6400_MAP

Id: 8/9 Title: File: MAP.kicad_sch Sheet: /MAP/


File: IGN6.kicad_sch Sheet: /Ignition/ rusefi.com

Id: 9/9 Title: UAEFI Ignition


Id: 9/9 Title: File: egt.kicad_sch Sheet: /EGT/

6 ABCD; ABCD Date: 2023-11-01 KiCad; E.D.A. 8.0.2 Size: A4; Rev:; Id: 10/9 Title: UAEFI Injector File: INJ6.kicad_sch Sheet: /Injector/ rusefi.comR³³ 4.7k GND R³⁴ 4.7k GND GND R³² 4.7k; GND R³¹ 4.7k R³⁰ 4.7k GND; R²⁹ 4.7k GND; 1 STATUS1; 3 STATUS2; U9 VNLD5160TR-E GND GND; U11 VNLD5160TR-E GND; U10 VNLD5160TR-E OUT6; IN5 OUT4 OUT3 OUT5 OUT2 OUT1; GND R³⁰ 4.7k; R³¹ 4.7k GND R³² 4.7k GND GND R³⁴ 4.7k; GND R²⁹ 4.7k GND R³³ 4.7k

Hellen One : Power-Module interface

Reverse polarity and overvoltage protection
F410 V12_RAW

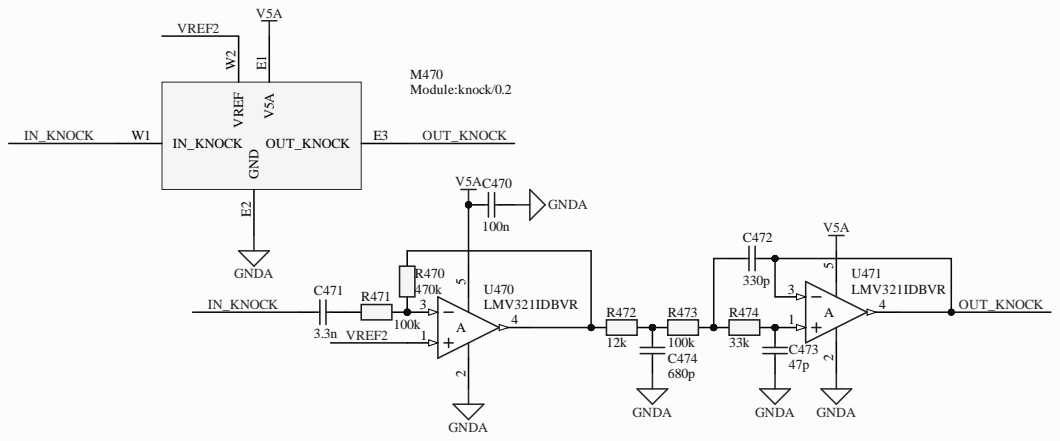
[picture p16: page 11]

# 6 U751 GND

1u R761

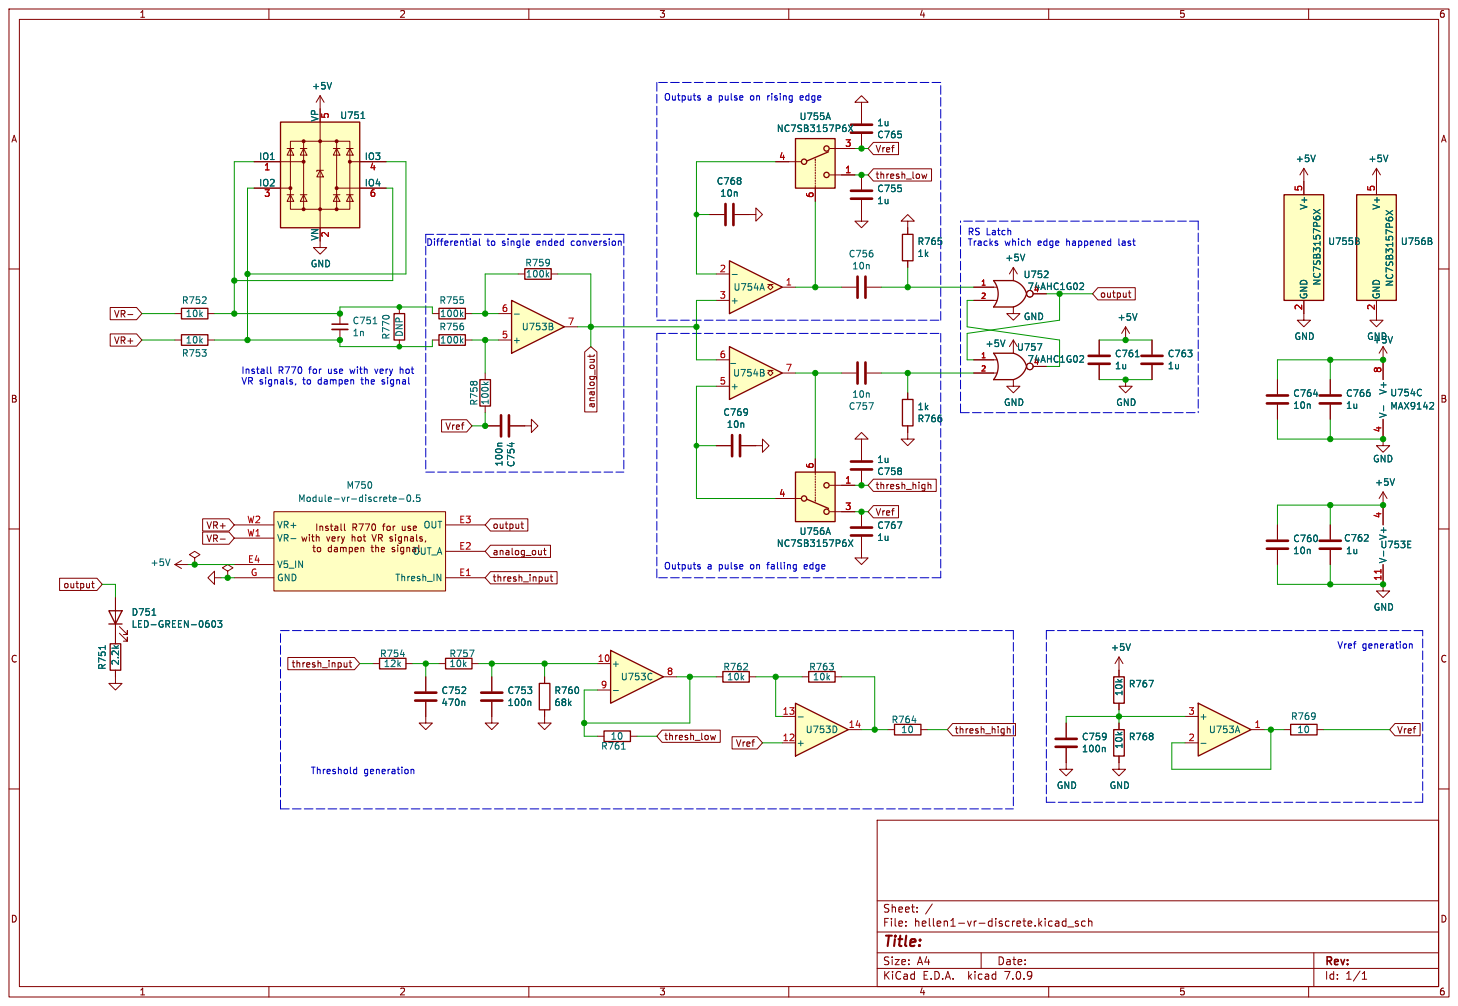
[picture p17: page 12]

Id: 1/1 Title: File: hellen1-vr-discrete.kicad_sch Sheet: /

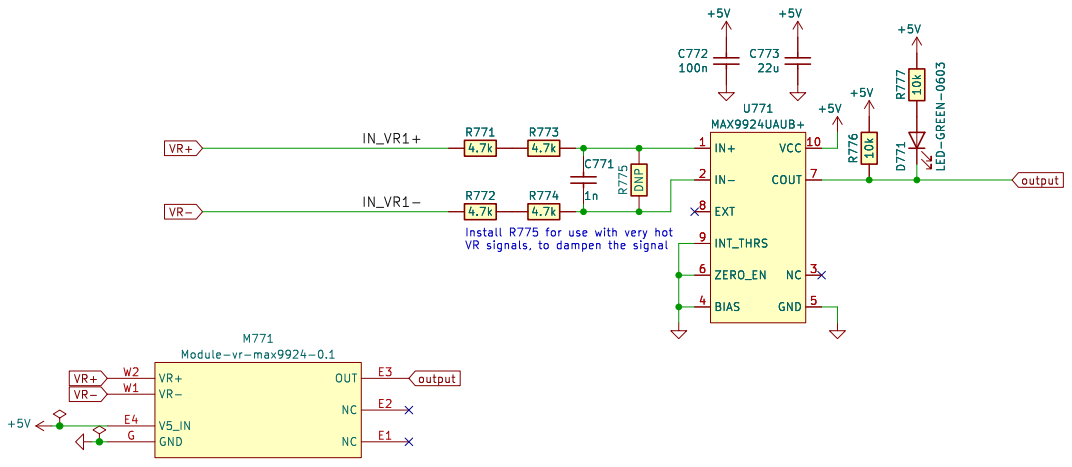
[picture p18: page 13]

File: hellen1-vr-max9924.kicad_sch Sheet: /
Id: 1/1 Title: VR MAX9924 module

+3.3V C616

27k +


100n GND GND R⁶⁰⁸ ⁴⁷

1 PA4 10 PA5 11 PA6 12 PA7 13 PB0 14 PB1 15 VSS 16 VDDIO2 17 PA8 18 PA9 19 PF0 2 PA10 20 PA11 21 PA12 22 PA13 23 PA14 24 PA15 25 PB3 26 PB4 27 PB5 28 PB6 29 PF1 3 PB7 30 PB8 31 VSSA 32 NRST 4 VDDA

1u GND GND GND
+3.3V R⁶¹¹ ²⁰k R⁶¹⁰ ²⁰k GND

to ground to improve the routing
(floating pins by the software).

Heater negative Power GND

VDDA GND
Nernst Sense Voltage Buffer Nernst Internal Resistance Measurement

+3.3V C606 DNP GND
File: hellen1-wbo.kicad_sch Sheet: / rusefi.com V⁻ 11 V⁺

Vdd 4; Vss 6; MCP6004; GNDA; OUT1; OUT2; OUT3; OUT4; C180 PIC18001 100n; PIC18002 COC3; PIR18001; PIR18002; PIR18003; PIR18004; PIR18005; PIR18006; PIR18007; PIR18008; COR5; PIR18101; PIR18102; PIR18103; PIR18105; PIR18104; PIR18106; PIR18107; PIR18108; COR6; PIU18001; PIU18002; PIU18003; PIU18004; PIU18005; PIU18006; PIU18007; PIU18008; PIU18009; PIU180010; PIU180011; PIU180012; PIU180013; PIU180014; COU2; PIC18001; POOUT2; POOUT1; POOUT3; POOUT4; POIN1; POIN3 PIU18005; PIU180010 POIN4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

Vdd 4; Vss 6; MCP6004; GNDA; OUT1; OUT2; OUT3; OUT4; C185 PIC18501 100n; PIC18502 COC3; PIR18501; PIR18502; PIR18503; PIR18504; PIR18505; PIR18506; PIR18507; PIR18508; COR5; PIR18601; PIR18602; PIR18603; PIR18605; PIR18604; PIR18606; PIR18607; PIR18608; COR6; PIU18501; PIU18502; PIU18503; PIU18504; PIU18505; PIU18506; PIU18507; PIU18508; PIU18509; PIU185010; PIU185011; PIU185012; PIU185013; PIU185014; COU2; PIC18501; POOUT2; POOUT1; POOUT3; POOUT4; POIN1; POIN3 PIU18505; PIU185010 POIN4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

SPI_; VCC; 5 SPI_SCK; 7 SPI_O; lex MicroSD; _MIS


R143 populated: analog input O2S
R145 populated: WAKEUP by CAN

*VIGN input is unprotected!
*A21 is duplicated for ADC and EINT



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

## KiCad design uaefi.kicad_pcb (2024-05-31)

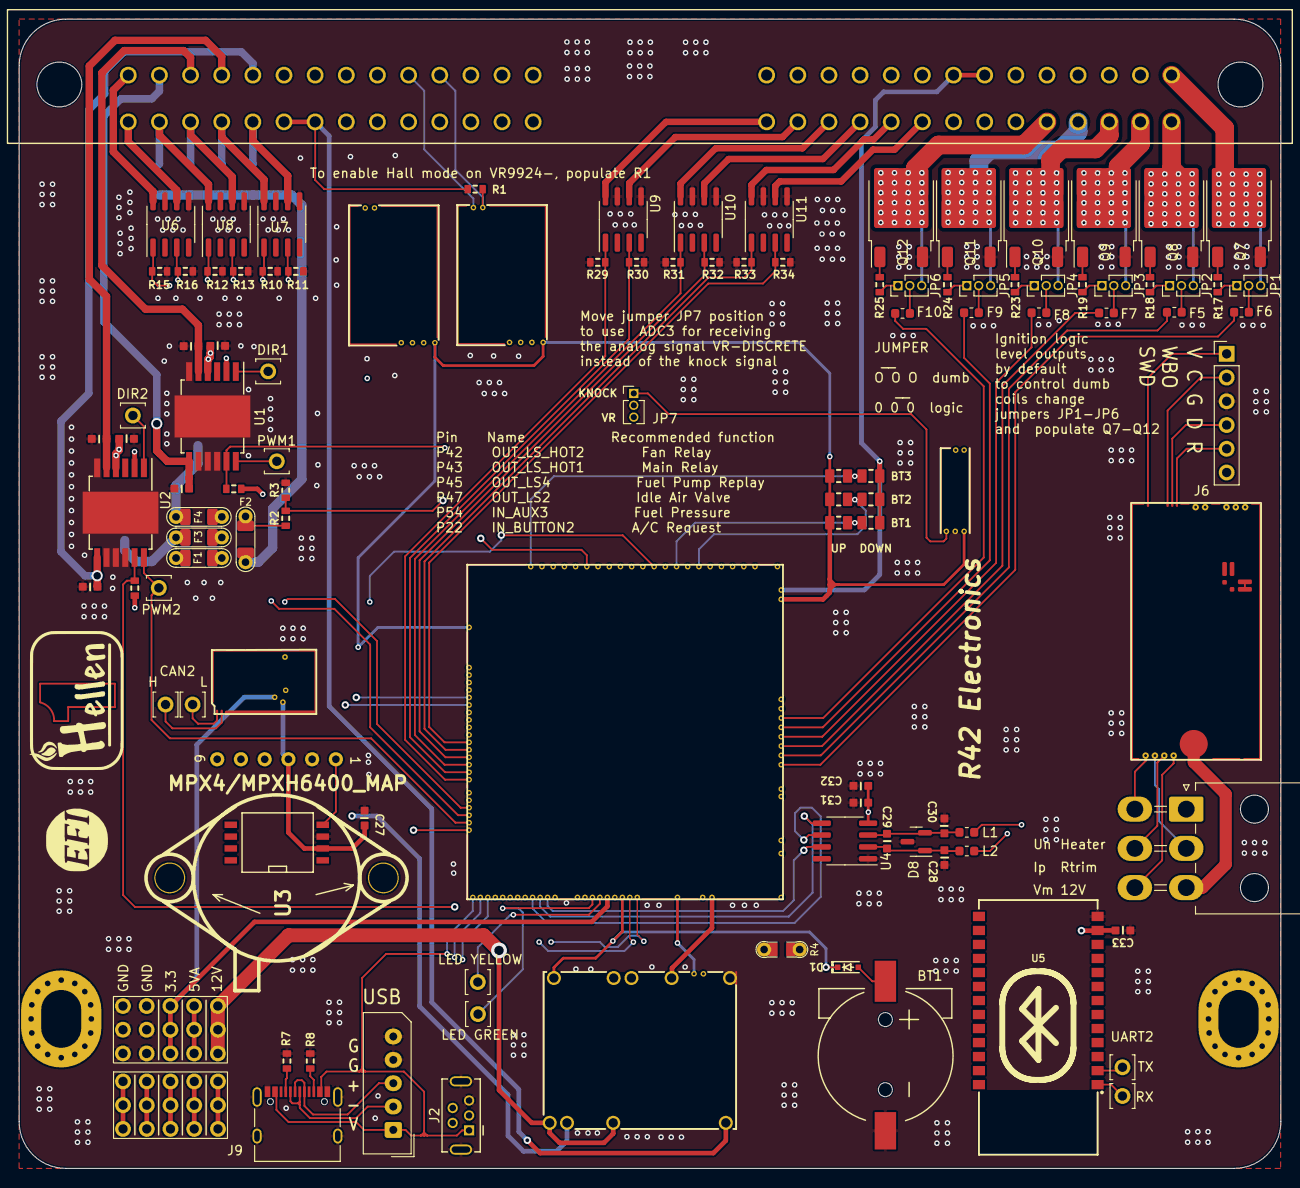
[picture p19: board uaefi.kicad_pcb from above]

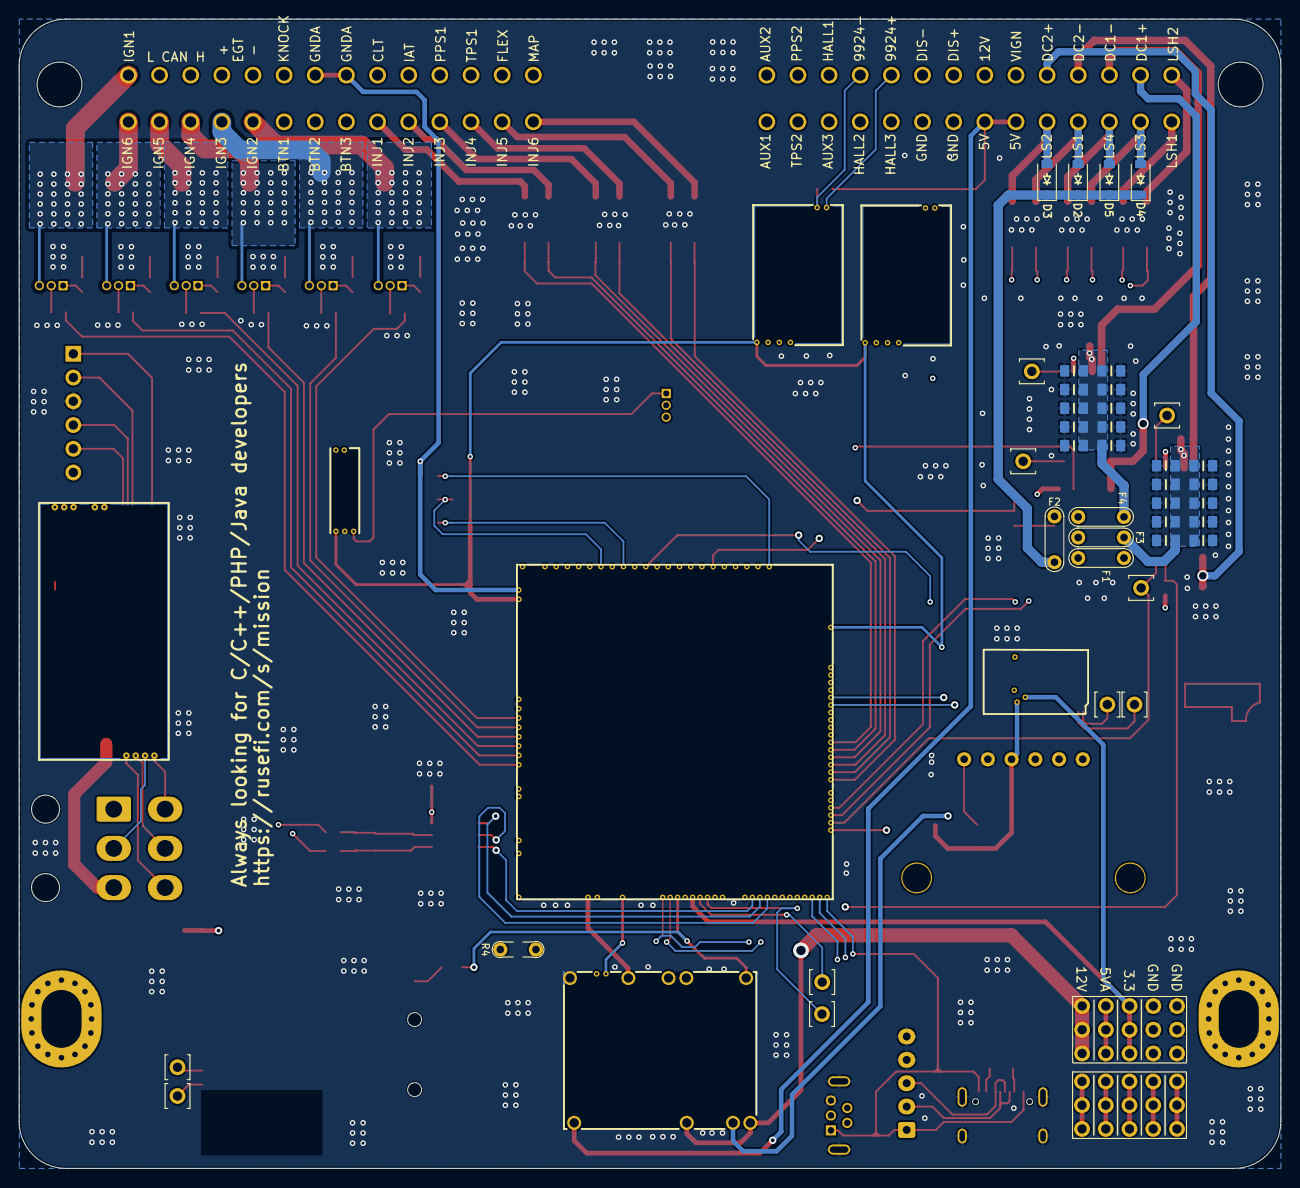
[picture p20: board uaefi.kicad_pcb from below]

Board: 4 copper layers, 135.0 x 123.0 mm, 137 parts (24 on the bottom side), 151 nets.

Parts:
BT1: CR1220; CR1220-2
C1, C2, C3, C4, C5, C6, C7, C8, C9, C10, C14, C15, C16, C17, C18, C19, C20, C21, C22, C23: 10u; C0805
C11, C24, C27, C29, C31, C33: 100n; C0603
C12, C13, C25, C26, C28, C30: 10n; C0603
C32: 1u; C0603
D1: 1N4148WS; SOD-323
D2, D3, D4, D5: B5819W; SOD-123
D8: NUP2105L; SOT-23
F1, F2, F3, F4: 12H1500D; PAD-1206-PAD
F5, F6, F7, F8, F9, F10: 50mA; Fuse_0603_1608Metric
G1: RUSEFI_LOGO; rusefi_logo
G2: LOGO
G3, G4: PROTO_AREA
H1: M4; MountingHole_4.3x6.2mm_M4_Pad_Via
H2: M3; MountingHole_4.3x6.2mm_M4_Pad_Via
J1: 211PL562L0011; 211PL562L0011_2
J2: USB_B_Mini; USB-MINI-B-VERTICAL
J3: 5569-06A2; Molex_Mini-Fit_Jr_5569-06A2_2x03_P4.20mm_Horizontal
J6: Conn_01x06; PinHeader_1x06_P2.54mm_Vertical
J7: Conn_01x05_Male; Molex_SPOX_5267-05A_1x05_P2.50mm_Vertical
J9: USB_C
JP1, JP2, JP3, JP4, JP5, JP6, JP7: Jumper_3_Open; PinHeader_1x03_P1.27mm_Vertical
L1, L2: 470R@100MHz; L_0603_1608Metric
M1: Module-power_12and5V-0.2; power_12and5V
M2: Module-knock-0.2; knock
M3: Module-vr-discrete-0.5; vr-discrete
M4: Module-vr-max9924-0.1; vr-max9924
M5: Module-wbo-0.5; wbo
M6: Module:mega-mcu100/0.3; mega-mcu100
M7: Module-can-0.1; can
P1, P2, P3, P4, P7, P8, P15, P16, P17, P18: Pad; PAD-TH
Q7, Q8, Q9, Q10, Q11, Q12: ISL9V3040D3ST; TO-252-2
R1, R9, R10, R11, R12, R13, R14, R15, R16, R29, R30, R31, R32, R33, R34: 4.7k; R0603
R2: 33k; R0603
R3: 6.8k; R0603
R4: Jumper-Pad-Pad; PAD-0805-PAD
R7, R8: 5.6k; R0603
R17, R18, R19, R23, R24, R25: 22; R0603
R35, R36, R37: 10k; R0805
R38, R39, R40: DNP; R0805
U1, U2: TLE9201SG; Infineon_PG-DSO-12-11
U3: MPX4/MPXH6400_MAP; MPX-4_MAP
U4: MAX31855KASA; SOIC-8_3.9x4.9mm_P1.27mm
U5: JDY-33
U6, U7, U8, U9, U10, U11: VNLD5160TR-E; SOIC-8_3.9x4.9mm_P1.27mm

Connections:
+3.3V: M6.N21 (V33), R9.2, R14.2, U1.2 (VSO), U2.2 (VSO)
+3.3VA: C31.2, C32.2, C33.2, G3.3, G3.8, G3.13, M6.N15 (V33_SWITCHABLE), M7.V2 (CAN_VIO), U4.4 (V_CC), U5.12 (3V3)
+5V: M1.E4 (V5), M6.N22 (VCC)
+5VA: C27.2, G3.4, G3.9, G3.14, M2.E1 (V5A), M3.E4 (V5_IN), M4.E4 (V5_IN), M5.W1 (V5_IN), M6.E1 (V5A_SWITCHABLE), M6.W2 (V5A_SWITCHABLE), M7.V1 (V5), R38.2, R39.2, R40.2, U3.3 (VCC)
+5VP: J1.P48 (48), J1.P49 (49), M1.V4 (5VP), R1.1
+12V: F2.1, F3.1, F4.1, J1.P37 (37), R2.2
+12V_RAW: D2.1 (K), D3.1 (K), D4.1 (K), D5.1 (K), F2.2, G3.5, G3.10, G3.15, J3.1, M1.V1 (V12_PERM), M1.V3 (V12_RAW)
/12V_KEY: F1.1, J1.P36 (36)
/ADC3: JP7.2 (C), M6.S15 (IN_KNOCK_(PA2))
/CAN+: J1.P3 (3), M5.W4 (CANH), M6.W11 (CANH)
/CAN-: J1.P2 (2), M5.W3 (CANL), M6.W12 (CANL)
/DC1_DIR: M6.E21 (OUT_PWM4_(PC8)), P15.1, U1.1 (DIR)
/DC1_DIS: M6.E8 (SPI2_MISO_(PB14)), R9.1, U1.11 (DIS)
/DC1_PWM: M6.E20 (OUT_PWM3_(PC7)), P17.1, U1.12 (PWM)
/DC2_DIR: M6.E9 (SPI2_MOSI_(PB15)), P16.1, U2.1 (DIR)
/DC2_DIS: M6.N4 (USBID_(PA10)), R14.1, U2.11 (DIS)
/DC2_PWM: M6.E22 (OUT_PWM5_(PC9)), P18.1, U2.12 (PWM)
/DC Driver 1/PWR: C1.2, C2.2, C3.2, C4.2, C5.2, C6.2, C7.2, C8.2, C9.2, C10.2, C11.2, F4.2, U1.4 (VS)
/DC Driver 2/PWR: C14.2, C15.2, C16.2, C17.2, C18.2, C19.2, C20.2, C21.2, C22.2, C23.2, C24.2, F3.2, U2.4 (VS)
/EGT+: J1.P4 (4), L1.1
/EGT-: J1.P5 (5), L2.1
/EGT/SPI_CS: M6.N9 (SPI3_CS_(PA15)), U4.6 (~CS)
/EGT/SPI_SCK: M6.N10 (SPI3_SCK_(PC10)), U4.5 (SCK)
/EGT/SPI_SO: M6.N11 (SPI3_MISO_(PC11)), U4.7 (SO)
/IGN1: F6.2, M6.W10 (IGN1_(PC13))
/IGN2: F5.2, M6.W9 (IGN2_(PE5))
/IGN3: F7.2, M6.W8 (IGN3_(PE4))
/IGN4: F8.2, M6.W7 (IGN4_(PE3))
/IGN5: F9.2, M6.W6 (IGN5_(PE2))
/IGN6: F10.2, M6.W5 (IGN6_(PB8))
/INJ1: M6.E17 (OUT_INJ1_(PD3)), R29.2, U9.1 (IN1)
/INJ2: M6.E16 (OUT_INJ2_(PA9)), R30.2, U9.3 (IN2)
/INJ3: M6.E15 (OUT_INJ3_(PD11)), R31.2, U10.1 (IN1)
/INJ4: M6.E14 (OUT_INJ4_(PD10)), R32.2, U10.3 (IN2)
/INJ5: M6.E13 (OUT_INJ5_(PD2)), R33.2, U11.1 (IN1)
/INJ6: M6.E12 (OUT_INJ6_(PA8)), R34.2, U11.3 (IN2)
/INTERNAL_MAP: M6.S12 (IN_MAP2_(PC1)), U3.1 (VOUT)
/IN_AUX1: J1.P56 (56), M6.S11 (IN_O2S_/_CAN_WAKEUP_(PA0))
/IN_AUX2: J1.P29 (29), M6.S10 (IN_O2S2_(PA1))
/IN_AUX3: J1.P54 (54), M6.S7 (IN_AUX3_(PA7))
/IN_BUTTON1: J1.P23 (23), M6.S14 (IN_CRANK_(PB1)), R35.2, R38.1
/IN_BUTTON2: J1.P22 (22), M6.S16 (IN_CAM_(PA6)), R36.2, R39.1
/IN_BUTTON3: J1.P21 (21), M6.S1 (IN_D4_(PE15)), R37.2, R40.1
/IN_CLT: J1.P9 (9), M6.S21 (IN_CLT_(PC2))
/IN_FLEX: J1.P13 (13), M6.S17 (IN_VSS_(PE11))
/IN_HALL1: J1.P31 (31), M6.S4 (IN_D1_(PE12))
/IN_HALL2: J1.P53 (53), M6.S3 (IN_D2_(PE13))
/IN_HALL3: J1.P52 (52), M6.S2 (IN_D3_(PE14))
/IN_IAT: J1.P10 (10), M6.S20 (IN_IAT_(PC3))
/IN_KNOCK: JP7.1 (A), M2.E3 (OUT_KNOCK)
/IN_KNOCK_RAW: J1.P6 (6), M2.W1 (IN_KNOCK)
/IN_MAP: J1.P14 (14), M6.S13 (IN_MAP1_(PC0))
/IN_PPS1: J1.P11 (11), M6.S19 (IN_PPS_(PA3))
/IN_PPS2: J1.P30 (30), M6.S8 (IN_AUX2_(PC4/PE9))
/IN_TPS1: J1.P12 (12), M6.S18 (IN_TPS_(PA4))
/IN_TPS2: J1.P55 (55), M6.S9 (IN_AUX1_(PB0))
/IN_VIGN: F1.2, M1.V2 (IN_VIGN)
/IN_VMAIN: M6.S6 (IN_AUX4_(PC5)), R2.1, R3.2
/LS1: M6.E11 (OUT_INJ7_(PD15)), R10.2, U7.1 (IN1)
/LS2: M6.E10 (OUT_INJ8_(PD12)), R11.2, U7.3 (IN2)
/LS3: M6.E18 (OUT_PWM1_(PD13)), R12.2, U8.1 (IN1)
/LS4: M6.E19 (OUT_PWM2_(PC6)), R13.2, U8.3 (IN2)
/LS_HOT1: M6.W4 (IGN7_(PB9)), R16.1, U6.3 (IN2)
/LS_HOT2: M6.W3 (IGN8_(PE6)), R15.1, U6.1 (IN1)
/OUT_DC1+: C13.2, J1.P41 (41), U1.7 (OUT2)
/OUT_DC1-: C12.2, J1.P40 (40), U1.5 (OUT1)
/OUT_DC2+: C26.2, J1.P38 (38), U2.7 (OUT2)
/OUT_DC2-: C25.2, J1.P39 (39), U2.5 (OUT1)
/OUT_IGN1: J1.P1 (1), JP1.3 (B), Q7.2 (C)
/OUT_IGN2: J1.P28 (28), JP2.3 (B), Q8.2 (C)
/OUT_IGN3: J1.P27 (27), JP3.3 (B), Q9.2 (C)
/OUT_IGN4: J1.P26 (26), JP4.3 (B), Q10.2 (C)
/OUT_IGN5: J1.P25 (25), JP5.3 (B), Q11.2 (C)
/OUT_IGN6: J1.P24 (24), JP6.3 (B), Q12.2 (C)
/OUT_INJ1: J1.P15 (15), U9.8 (D1)
/OUT_INJ2: J1.P16 (16), U9.6 (D2)
/OUT_INJ3: J1.P17 (17), U10.8 (D1)
/OUT_INJ4: J1.P18 (18), U10.6 (D2)
/OUT_INJ5: J1.P19 (19), U11.8 (D1)
/OUT_INJ6: J1.P20 (20), U11.6 (D2)
/OUT_LS1: D2.2 (A), J1.P46 (46), U7.8 (D1)
/OUT_LS2: D3.2 (A), J1.P47 (47), U7.6 (D2)
/OUT_LS3: D4.2 (A), J1.P44 (44), U8.8 (D1)
/OUT_LS4: D5.2 (A), J1.P45 (45), U8.6 (D2)
/OUT_LS_HOT1: J1.P43 (43), U6.6 (D2)
/OUT_LS_HOT2: J1.P42 (42), U6.8 (D1)
/PG_5VP: M6.N12 (SPI3_MOSI_(PC12)), R4.2
/PWR_EN: M1.E5 (EN_5VP), M6.N20 (OUT_PWR_EN_(PE10))
/USB+: J2.3 (D+), J7.3, J9.A6 (D+), J9.B6 (D+), M6.N3 (USBP_(PA12))
/USB-: J2.2 (D-), J7.2, J9.A7 (D-), J9.B7 (D-), M6.N2 (USBM_(PA11))
/VBAT: D1.1 (K), M1.E1 (VBAT), M6.N17 (VBAT)
/VBUS: J2.1 (VBUS), J7.1, J9.A4 (VBUS), J9.A9 (VBUS), J9.B4 (VBUS), J9.B9 (VBUS), M6.N1 (VBUS)
/VIGN: M1.E3 (VIGN), M6.E5 (IN_VIGN_(PA5))
/VREF1: M2.W2 (VREF), M6.S22 (VREF1)
/VR_DISCRETE: M3.E3 (OUT), M6.N18 (UART8_RX_(PE0))
/VR_DISCRETE+: J1.P35 (35), M3.W2 (VR+)
/VR_DISCRETE-: J1.P34 (34), M3.W1 (VR-)
/VR_DISCRETE_A: JP7.3 (B), M3.E2 (OUT_A)
/VR_DISCRETE_THR: M3.E1 (Thresh_IN), M6.E23 (OUT_PWM6_(PD14))
/VR_MAX9924: M4.E3 (OUT), M6.N19 (UART8_TX_(PE1))
/VR_MAX9924+: J1.P33 (33), M4.W2 (VR+)
/VR_MAX9924-: J1.P32 (32), M4.W1 (VR-), R1.2
/WBO_Heater: J3.3, M5.E5 (LSU_H+)
/WBO_Ip: J3.5, M5.E3 (LSU_Ip)
/WBO_Rtrim: J3.2, M5.E4 (LSU_Rtrim)
/WBO_Un: J3.4, M5.E1 (LSU_Un)
/WBO_Vm: J3.6, M5.E2 (LSU_Vm)
GND: BT1.2 (-), C1.1, C2.1, C3.1, C4.1, C5.1, C6.1, C7.1, C8.1, C9.1, C10.1, C11.1, C12.1, C13.1, C14.1, C15.1, C16.1, C17.1, C18.1, C19.1, C20.1, C21.1, C22.1, C23.1, C24.1, C25.1, C26.1, C27.1, C28.1, C30.1, C31.1, C32.1, C33.1, D8.3 (A), G3.1, G3.2, G3.6, G3.7, G3.11, G3.12, J1.P50 (50), J1.P51 (51), J2.5 (GND), J2.6 (Shield), J6.3, J7.4, J7.5, J9.A1 (GND), J9.A12 (GND), J9.B1 (GND), J9.B12 (GND), J9.S1 (SHIELD), M1.S1 (GND), M2.E2 (GND), M3.G (GND), M4.G (GND), M5.E6 (LSU_H-), M5.G (GND), M6.G (GND), M7.E1 (GND), Q7.3 (E), Q8.3 (E), Q9.3 (E), Q10.3 (E), Q11.3 (E), Q12.3 (E), R3.1, R7.1, R8.1, R10.1, R11.1, R12.1, R13.1, R15.2, R16.2, R29.1, R30.1, R31.1, R32.1, R33.1, R34.1, U1.6 (GND), U1.8 (SI), U1.9 (CSN), U1.10 (SCK), U1.13 (GND), U2.6 (GND), U2.8 (SI), U2.9 (CSN), U2.10 (SCK), U2.13 (GND), U3.2 (GND), U4.1 (GND), U5.13 (GND), U6.5 (S2), U6.7 (S1), U7.5 (S2), U7.7 (S1), U8.5 (S2), U8.7 (S1), U9.5 (S2), U9.7 (S1), U10.5 (S2), U10.7 (S1), U11.5 (S2), U11.7 (S1)
GNDA: J1.P7 (7), J1.P8 (8), M6.W1 (GNDA), R35.1, R36.1, R37.1
unnamed: BT1.1 (+), D1.2 (A)
unnamed: G4.1, G4.6, G4.11
unnamed: G4.5, G4.10, G4.15
unnamed: G4.2, G4.7, G4.12
unnamed: G4.3, G4.8, G4.13
unnamed: G4.4, G4.9, G4.14
unnamed: J6.1, M5.W8 (V33_OUT)
unnamed: J6.2, M5.W7 (SWCLK)
unnamed: J6.4, M5.W6 (SWDIO)
unnamed: J6.5, M5.W5 (nReset)
unnamed: J9.A5 (CC1), R7.2
unnamed: J9.B5 (CC2), R8.2
unnamed: JP1.1 (A), R17.2
unnamed: F6.1, JP1.2 (C)
unnamed: JP2.1 (A), R18.2
unnamed: F5.1, JP2.2 (C)
unnamed: JP3.1 (A), R19.2
unnamed: F7.1, JP3.2 (C)
unnamed: JP4.1 (A), R23.2
unnamed: F8.1, JP4.2 (C)
unnamed: JP5.1 (A), R24.2
unnamed: F9.1, JP5.2 (C)
unnamed: JP6.1 (A), R25.2
unnamed: F10.1, JP6.2 (C)
unnamed: M1.E6 (PG_5VP), R4.1
unnamed: M5.J1 (SEL1), M5.J_GND1 (PULL_DOWN1)
unnamed: M6.N14a (LED_GREEN), P4.1
unnamed: M6.N14b (LED_YELLOW), P3.1
unnamed: M6.E6 (SPI2_CS_/_CAN2_RX_(PB12)), M7.V6 (CAN_RX)
unnamed: M6.E7 (SPI2_SCK_/_CAN2_TX_(PB13)), M7.V5 (CAN_TX)
unnamed: M6.N14 (UART2_RX_(PD6)), P7.1, U5.1 (TXD)
unnamed: M6.N13 (UART2_TX_(PD5)), P8.1, U5.2 (RXD)
unnamed: M7.S2 (CANH), P2.1
unnamed: M7.S1 (CANL), P1.1
unnamed: Q7.1 (G), R17.1
unnamed: Q8.1 (G), R18.1
unnamed: Q9.1 (G), R19.1
unnamed: Q10.1 (G), R23.1
unnamed: Q11.1 (G), R24.1
unnamed: Q12.1 (G), R25.1
unnamed: C29.2, C30.2, D8.2 (K), L1.2, U4.3 (T+)
unnamed: C28.2, C29.1, D8.1 (K), L2.2, U4.2 (T-)

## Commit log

2024-05-16 [skip actions] Auto-generated board v2.1
    [uaefi-B_Cu.gbl, uaefi-B_Mask.gbs, uaefi-B_Paste.gbp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]
2024-05-16 Reev.D update
    [uaefi.kicad_pcb, uaefi.kicad_sch]
2024-05-18 Rev.D update
    [uaefi.kicad_pcb, uaefi.kicad_sch]
2024-05-24 Add Heatsink
    [uaefi.kicad_pcb]
